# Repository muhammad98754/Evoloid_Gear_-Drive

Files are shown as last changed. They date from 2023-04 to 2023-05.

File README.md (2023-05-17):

# Evoloid_Gear_-Drive (LUA language) --3D printing
3D Printing with IceSL Slicer and Modeler Using LUA Programming

Project: High Gear Ratio Evoloid Gear Drive Development

•Designed and created a high gear ratio Evoloid gear drive using IceSL modeler and slicer and LUA scripting language, utilizing 3D printing to achieve precise and accurate results.

•Produced a final gear assembly by generating an STL file using IceSL slicer and printing it using FDM 3D printing technology, demonstrating proficiency in designing and manufacturing complex mechanical systems

The coding for this project was written in LUA programming language, and I utilized ICeSL Modeler and Slicer for the implementation. I was able to generate an STL file using ICeSL Slicer, which could be later used as a G-code provider for FDM printers. Finally, the assembled gear was successfully printed at the designated site.

                                   Evoloid high gear ratio drive mechanism
                                   


                       changing the  tweak,we can rotate the  high gear ratio evoloid drive mechanism
                       
2023-05-17 (2)

                                    simple spur gear drive mechanism
                                    
2023-05-17 (3)

                               high gear ratio evoloid gear drive assembly
                               
2023-05-17 (4)

2023-05-17 (6)

2023-05-17 (7)

              base plate and screw system to make the final assembly which will print using FDM 3D printing system
              
2023-05-17 (5)

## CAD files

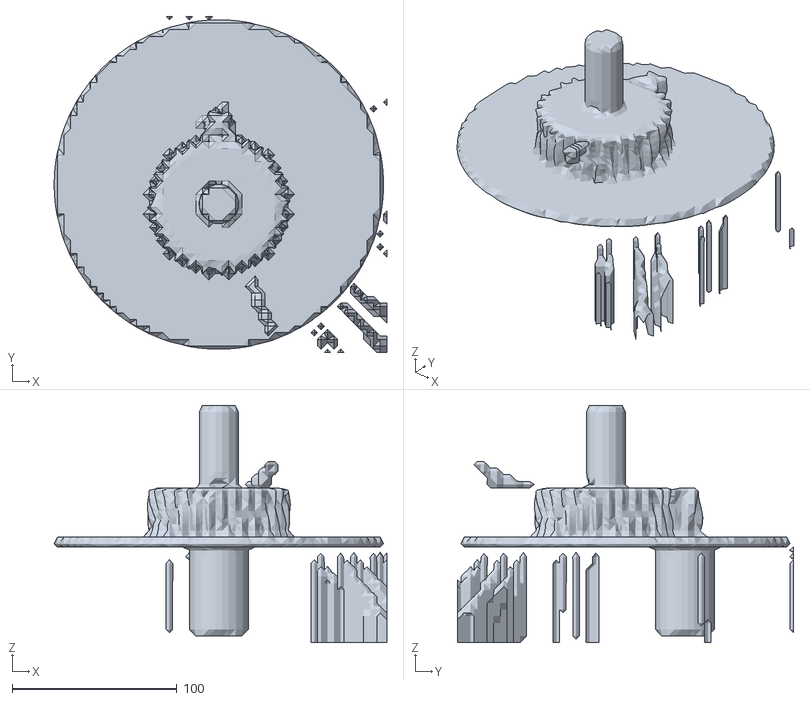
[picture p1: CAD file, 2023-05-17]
EvoloidSTL.stl
202.0 x 204.0 x 144.0

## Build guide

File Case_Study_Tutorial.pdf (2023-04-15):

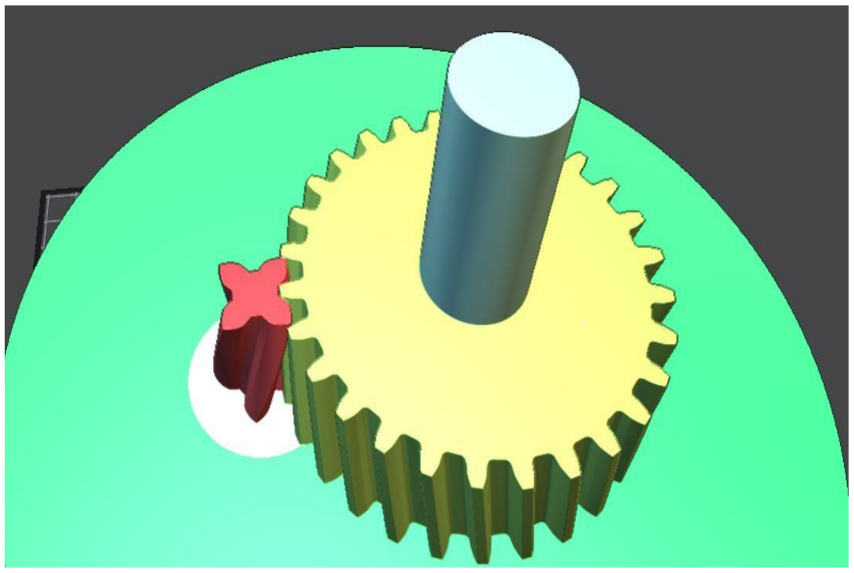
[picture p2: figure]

1 | P a g e

## Case Study Cyber-Physical Production System

## Using AM

## Instructions to Print the High Ratio Evoloid Drive

Group: Gear Mechanism Using AM
Supervisor: Prof.Dr.Ing.Stefan Scherbarth (Head of the mechatronics and cyber-physical systems department at DIT University, Deggendorf)

By Muhammad Safeer – 22103086

Date: 12th June 2022

2 | P a g e

3 | P a g e

## Table of Contents

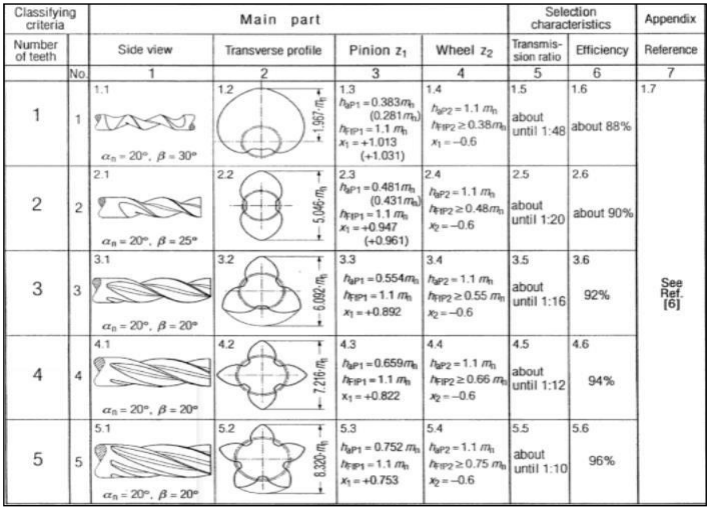
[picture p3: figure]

4 | P a g e

## 1 Introduction

Evoloid drive systems are helical cut pairs of gears with number of teeth less than 7 at the pinion or driver enabling the design of compact powerful gears. This system has high load capacity, and it can achieve a high gear ratio in a single stage. For more information, visit the Technical Report “Involute Gearing: Evoloid Drive with High Gear Ratio”.

- In this document, necessary information to replicate the display model(high gear ratio evoloid drive) with AM with the help of Lua script in IceSl is stated.
- Evoloid Gears are helical cut pairs of gears with number of teeth less than 7 at the pinion which in turn allows to attain a high gear ratio in a single stage.
- Users can easily modify the Evoloid drive by changing the UI box Input parameters like number of teeth on pinion and gear, module, helix angle, face width, profile shift, addendum and dedendum modification coefficients of both pinion and gear.
- Users should provide the input variables like pressure angle, helix angle, number of teeth on pinion, profile shift and addendum, dedendum modification coefficients for both pinion and gear according to the table for different high gear ratio. (Chakarabarthi)
- We assume that the user has sufficient knowledge about AM, Lua and IceSl.
- The LUA script description along with the STL file generation is also included in this document.

Figure 1:Evoloid drive input parameters with respect to different high gear ratio values (Chakarabarthi)

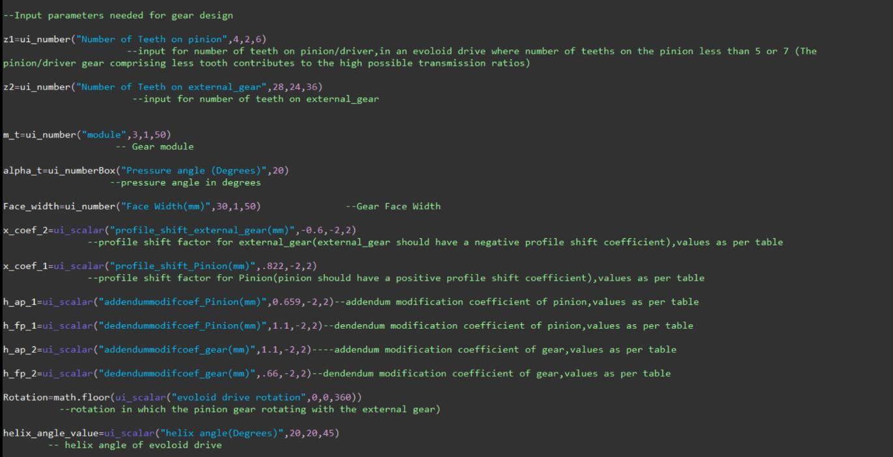
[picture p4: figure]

5 | P a g e

## 2 IceSL Software

IceSL is an advanced tool which helps in designing complex models for 3D printing. The app comes with a slicer that generates precise instructions to be used by all sorts of printers. Modelling in IceSl is done with the help of Lua Script. Modelling of the different shapes are done with customization of parameters. The application comes with two different software, namely the Forge and Slicer. Slicer is a tool that focuses on generating accurate instructions forthe printer, the Forge is where we can design and customise models. For more information visit [IceSL (loria.fr)]. (https://icesl.loria.fr/)

## 3 Input parameters

The first step in creating an Evoloid drive in IceSL is to define the basic parameters for the gear. Some of these parameters are user defined and the other parameters are derived from the inputs given. Through the tweak box the user can change the parametric valuesto analyse the variations in the model. There are two gears designed in the script so that the user must change the parameter of both gears. The important thing is that parameters like number of teeth ,helix angle, pressure angle, profile shift, addendum and dedendum modification coefficients of both pinion and gear should be according with the table values (Chakarabarthi).For more information about how to create a tweak box visit [Scripting language · Wiki · mfx / IceSL documentation · GitLab (inria.fr)]. (https://gitlab.inria.fr/mfx/icesl-documentation/-/wikis/Scripting-language#tweaks)

The input parameters needed for gear design are defined as a user interface in the following way:

Figure 2:Input parameters for gear design (Chakarabarthi)

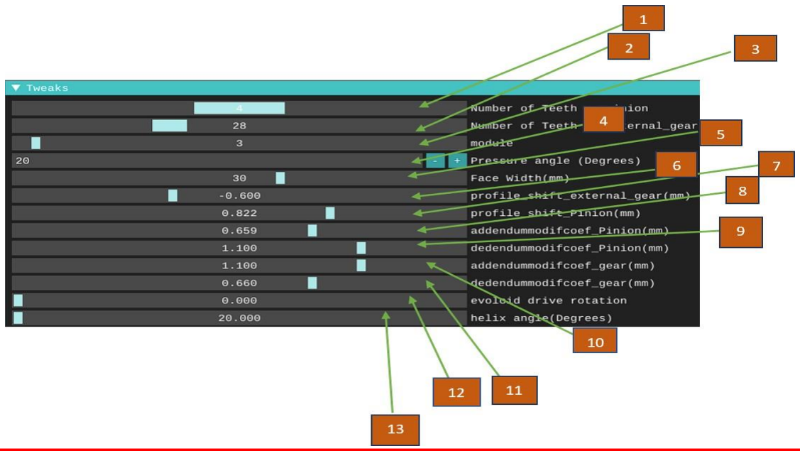
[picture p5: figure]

6 | P a g e

The tweak box explained in detail below:

Figure 2.1:Tweak box for the input parameters needed for gear design (Chakarabarthi)

As shown above, users can easily modify the model by changing the input parameters in the tweak box. Each number here represents the input data and described below in detail.

1. For the evoloid drive the number of teeth on the pinion should be lessthan seven. less number of teeth provide high gear ratio. Slide the sliderto change the number of teeth on pinion, values as per the table .
2. With this option users can change the number of teeth on big gear, values as per the table.
3. With this option users can change the module of both gears which make the gears bigger /smaller
4. Slide the slider to change the pressure angle of both gears. values as per the table.
5. With this option users can change the face width/thickness of both gears
6. Slide the slider to change the profile shift of big gear, values as per the table.
7. Slide the slider to change the profile shift of pinion/gear with a small number of teeth, values as per the table.
8. With this option users can change the addendum modification coefficients of Pinion, values as per the table.
9. With this option users can change the dedendum modification coefficients of Pinion, values as per the table.
10. With this option users can change the addendum modification coefficients of big gear, values as per the table.

7 | P a g e
11. With this option users can change the dedendum modification coefficients of big gear, values as per the table.
12. Slide the slider to rotate both gears so that meshing takes place.
13. With this option users can change the helix angle of both gears, values as per the table.

## 4 Script Description

We have parametrically designed the high gear ratio evoloid drive mechanism consisting of a big gear and a pinion with small number of teeth. The assembly consists of meshing of both pinion and big gear where the gears are helical toothed. To get the proper mesh, the input parameters should follow the table values (Chakarabarthi). Important steps in creating the model are described below.

- Step 1: Defined the input parameters for the gear design by UI variables. Line number 14-46.[For more information check the Lua code].
- Step 2: Created a function called gear()[line number 52-178] to generate the involute full spur gear profile and inside the function we have created many sub functions.[For more information check the Lua code].sub functions are described below.
1. function involute(r_b, angle)[line number 114-116]-this involute function generates the involute tooth geometry which gives x and y components of points in return
2. function involute_mirror(involut_points)[line number 119-121]-this function gives the mirror points of any contour concerning the y-axis
3. function curve(r_1,r_2)[line number 95-97]-this function responsible to find the right angle between both sides of the Gear
4. function point_rotate(ang, points)[line number 144-146]-this function responsible for the rotation of whole tooth around z axis
5. function circle(a,b,r,th)[line number 148-150]-function to create a circle
6. function slope(contour)[line number 109-111]-thisfunction find the slope of at the of contour
7. function extrude(Contour, angle, dir_v, scale_v, z_steps)[line number 183-236]-this function extrudes the gear at a helix angle (Prof.Dr.Ing.Stefan Scherbarth).
8. function helicalangle(Face_width,z,m_t,helix_angle_value)[line number 239-243]-function to calculate the helix angle
9. function gearangle(m_t,x_coef,alpha_t,z)[line number 254-257]-this function calculate angle of both sides of tooth
10. emit(translate(0,-d_p/2,0)*Evoloid_gear,10)[line number 287]-emitting the big gear
11. emit(translate(0,-d_p/2,-Face_width)*rotation_2*difference(shaft,cube),12)[line number 293]-emitting the shaft for big gear

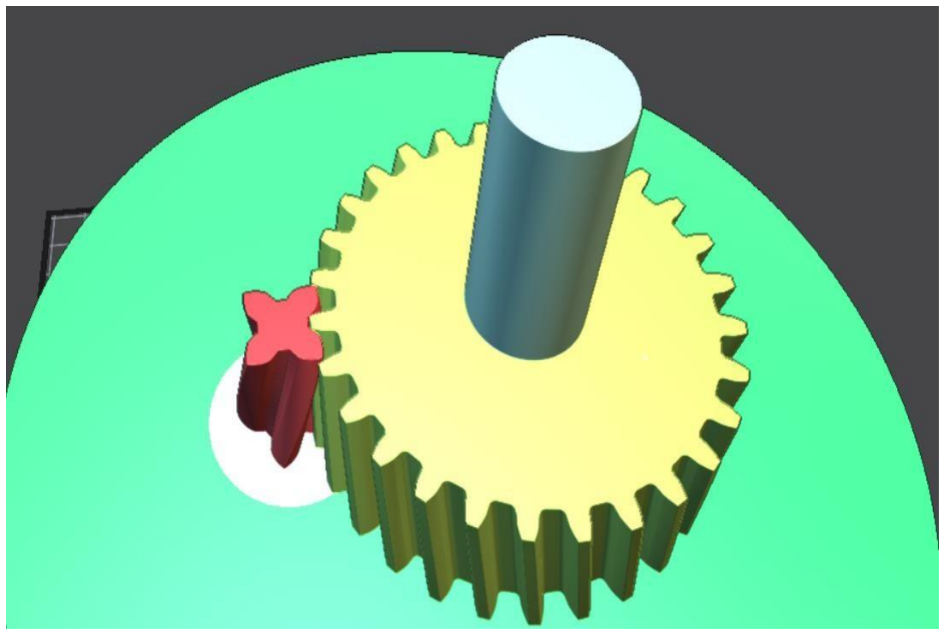
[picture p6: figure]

8 | P a g e
12. emit(translate(0,-value_1*2.53,-Face_width-6)*difference(casing_base,hole_cylinder),19)[line number 300]-emitting the casing base [For more information check the Lua code].
- Step 3: Finally, by using the extrude function(Code Line number 182-235,(Prof.Dr.Ing.Stefan Scherbarth) we can extrude the gear at a helix angle so that helical gear can be generated. Then emitting both gears. Important is input parameters like number of teeth, helix angle, pressure angle, addendum and dedendum, profile shift factors should be based on the table. [For more information check the Lua code]

The Lua code has been included with many commentsso that users can easily understand the above steps in detail while checking the code.

## 5 Output

The output of our Lua script in IceSL is shown below:

Figure 3:High Ratio Evoloid drive assembly

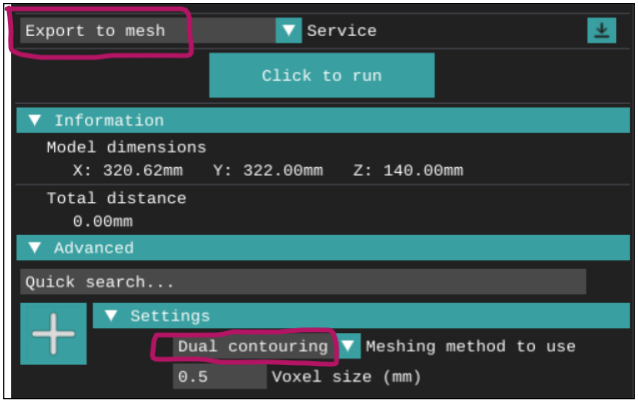
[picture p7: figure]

9 | P a g e

## 6 STL file generation and Slicing

To print the evoloid drive assembly, first the user must generate an STL file. For more information user can check here,[Slicing settings (loria.fr)]. (https://icesl.loria.fr/parameters/) In a nutshell user can create an STL file as shown below,

Figure 4:STL file generation

- User needs to select “Export to mesh” under the service tab.
- User needs to choose “Dual contouring” under the tab Meshing method to use.
- User can change the Voxel size

After the STL file generation, the user must slice it to generate the G-code. Before that user must select the printer, material etc. From the settings user can change many factors. After generating the G-code user can check the print time(build time),number of layers and many more.

## 7 Assembly Description

Part list:

1. Big Gear
2. Pinion
3. Shaft for Big gear
4. Shaft for Pinion
5. Casing for the assembly 6.Bolts/Nuts

10 | P a g
- The high gear ratio Evoloid drive mechanism can be printed by the user by following the instructions. For the Assembly, a part list is also stated above so that the user can assemble the mechanism.
- The Big Gear and pinion are mounted on the casing using the 4 bolts so that the user needs to drill holes. A shaft is also mounted on the slot of the big gear. For the pinion shaft to fit the pinion in the casing we must cut the casing or drill a hole in casing.

## 8 Credits

- Chakarabarthi, A. (n.d.). Engineering Design Synthesis: Understanding, Approaches and Tools. .[Engineering Design Synthesis: Understanding, Approaches and Tools -Google Books] (https://books.google.de/books?id=IUiTdfVxJHwC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)
- Gmbh, M.-K. (n.d.).
- Prof.Dr. Ing. Stefan.Scherbarth, P. (n.d.). for the extrude function in the Lua script (Code Line number 182-235),[For more information check the Lua code]

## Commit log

2023-04-15 Create High gear ratio --Evoloid gear drive
    Created a 3D model of Evoloid helical gear drive using ICESL modeler and slicer and LUA scripting language, to ensure that the gear design is accurate and optimized for manufacturing.
    • Created an STL file using the ICESL slicer to produce the final gear assembly
    • Printed the final gear drive by using FDM 3D printer (Fused deposition modelling)
2023-04-15 Add files via upload
    screenshots for the assembly model
2023-05-16 Rename High gear ratio --Evoloid gear drive to High gear ratio --Evoloid gear drive.lua
2023-05-17 Rename screw plus base.txt to screw plus base.lua
2023-05-17 Rename evoloid gear drive final assembly.txt to evoloid gear drive final assembly.lua
